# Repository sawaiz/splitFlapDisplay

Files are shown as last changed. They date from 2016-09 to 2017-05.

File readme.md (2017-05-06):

# Split Flap Display
Train stations and airports used to be riddled with these before LCD displays and monitors became commonplace. They used to show the departing and arrival scheduled as well as any delays but they fell out of favour due to the ease and creativity afforded with newer display technologies. What you lose along with that is the riffle sound that draws the eye when something changes, low power consumption, and unsurpassed visibility.

They are also referred to by genericised trademarks such as *Solari boards* after Solari di Udine, or *Pragoton* after the Czech manufacturer. New ones are no longer made and old ones under heavy disuse seldom show up on eBay and cost in the thousands per character, for a likely non-working one.

This project acts as a modern, modular, easy to interface alternative to finding vintage terminal displays. The goal is to have medium run (~100) production costs to near 10-15 USD/module.

## Module
The frame is laser cut acrylic, thickness is kept low and with a few modifications it can be made to injection mould and snap together. Currently, solvent welded. Electronics are mounded with screws, and communication occurs through pogo pins. Magnets connect modules to each other, and their polarity and positioning make sure it can only be plugged in properly. A magnet is also on the great wheel and is used for homing.

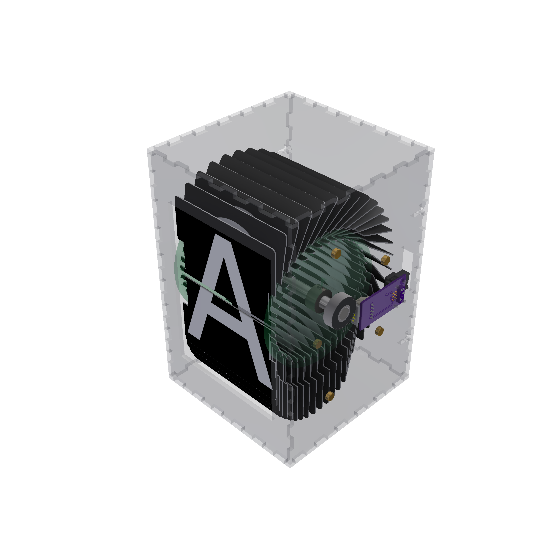
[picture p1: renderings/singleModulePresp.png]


The male pins can be seen on this side along with the gears, motor and main hub. Main shaft is mounted in inexpensive skateboard bearings and gears are those popularised by 3D printers, therefore prices are always falling. GT2 belts, collar clamps and 8mm hardened shaft also fall under that category.

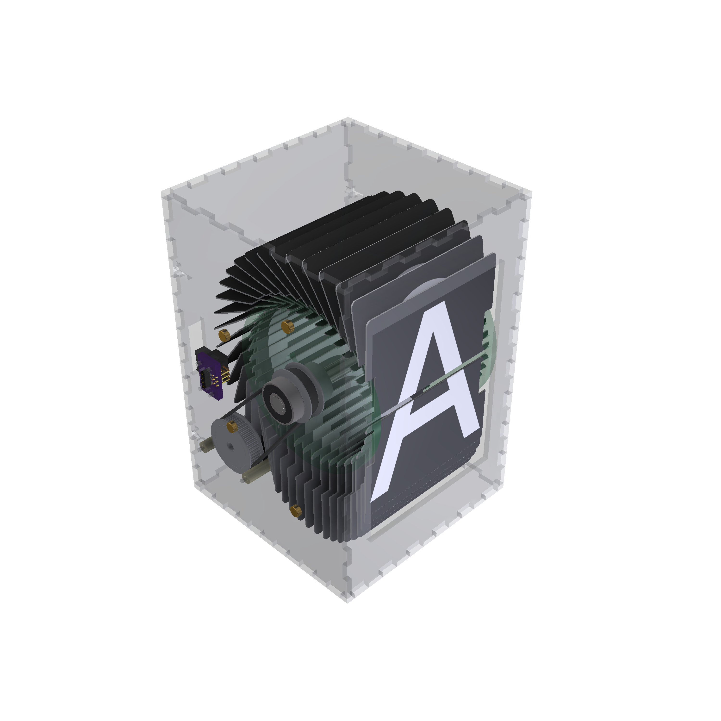
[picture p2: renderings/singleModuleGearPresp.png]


The "flaps" are based on die cut notches in plastic card blanks. Many vendors will print and die cut large quantities of cards, making scaling simple and labour intensive. Font and spacing can be changed, but as the goal is visibility, a san-serif monospaced font should be used. 

## Electronics
PCB and layout files found under electronics. Runs on a ATtiny13A, hall sensor for angular feedback, and a Darlington array for controlling the stepper. Under 5 USD in parts for medium volumes including the motor and pogo pins.

The two boards, in/out are connected with a ribbon able and IDC connectors (think PATA hard drives), inexpensive, easy to crimp... and even available pre-crimped in 4/6" lengths.

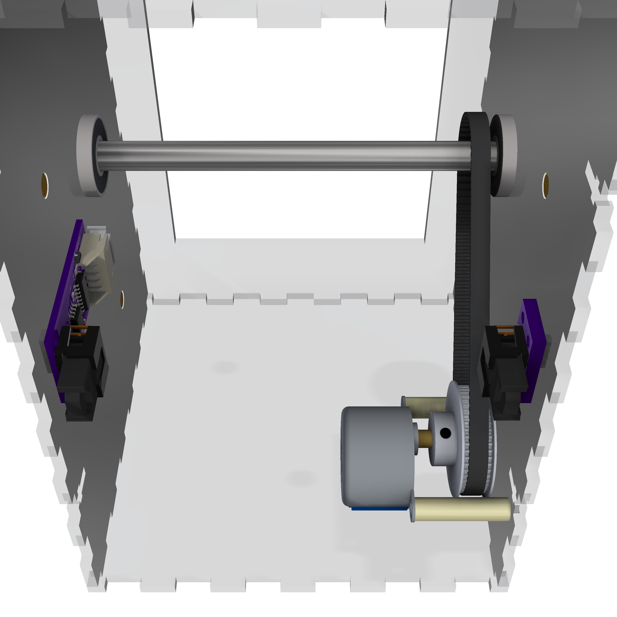
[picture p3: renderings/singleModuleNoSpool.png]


TODO: Schematic/layout images, BOM

### Firmware
AVR firmware along with makefile under firmware directory. On start it rotates to home, and then acts as a shift register forwarding the last character given

TODO: Insert communication clock diagram
TODO: Walk through code, decently commented, but avr ports are confusing

[singleModulePresp]: renderings/singleModulePresp.png "Assembled view"
[singleModuleGearPresp]: renderings/singleModuleGearPresp.png "Gear side view"
[singleModuleNoSpool]: renderings/singleModuleNoSpool.png "Detail of electronics with spool removed"

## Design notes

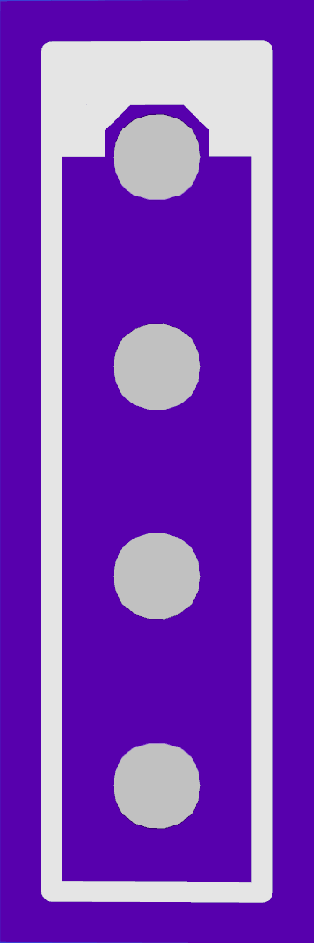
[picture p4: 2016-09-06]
electronics/cad/landing/back.png

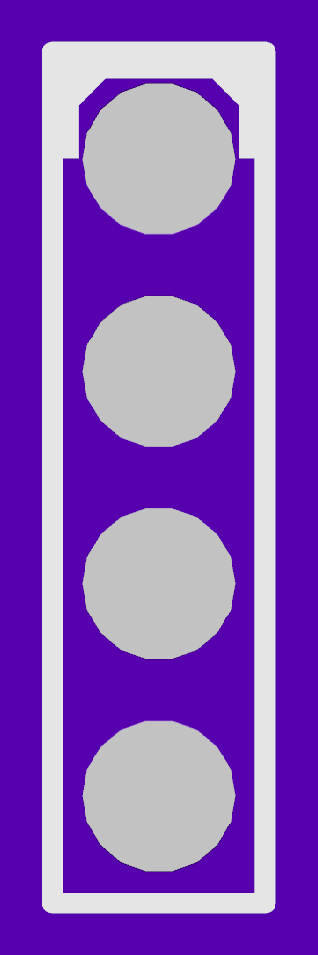
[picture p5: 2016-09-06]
electronics/cad/landing/front.png

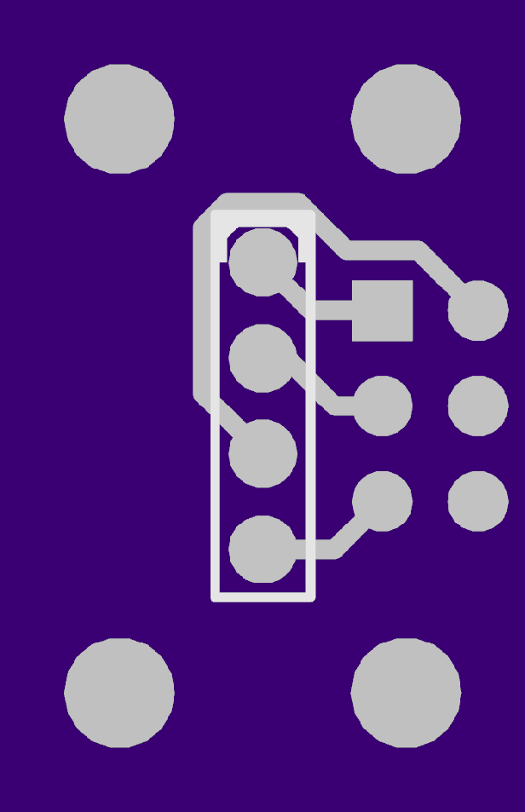
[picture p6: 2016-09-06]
electronics/cad/spring/back.png

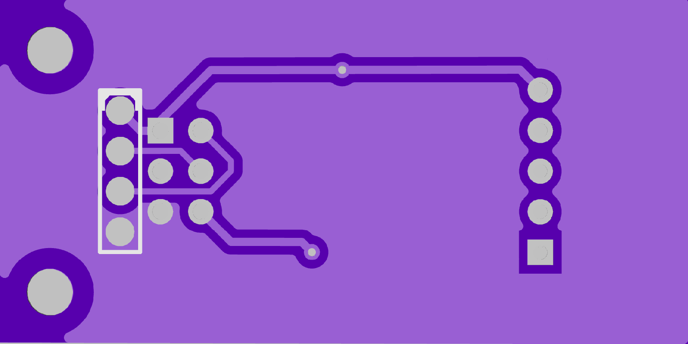
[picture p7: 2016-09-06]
electronics/cad/uC/back.png

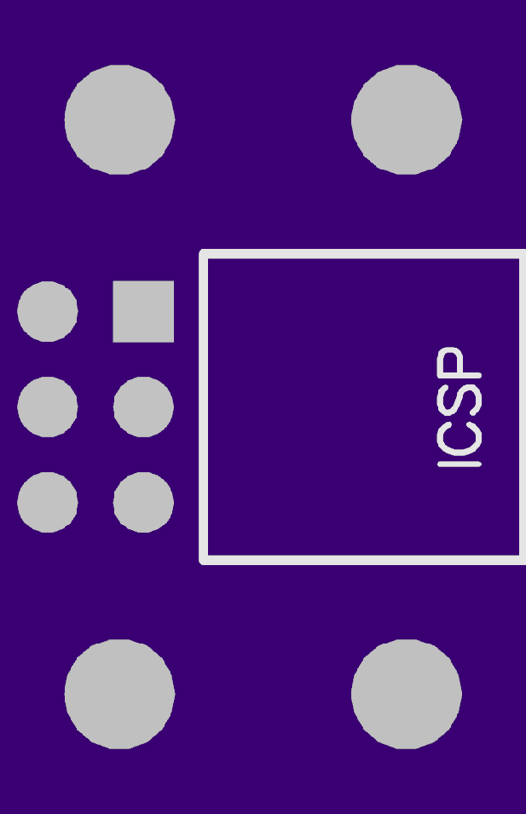
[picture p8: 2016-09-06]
electronics/cad/spring/front.png

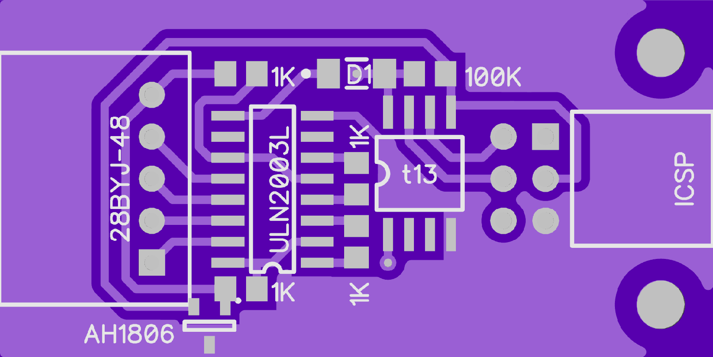
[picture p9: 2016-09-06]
electronics/cad/uC/front.png

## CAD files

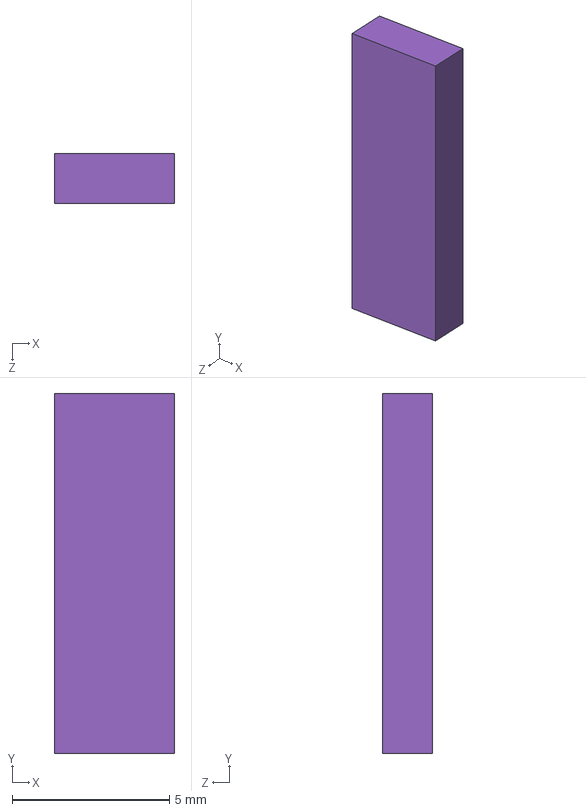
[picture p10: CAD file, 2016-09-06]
electronics/cad/landing/landing.step
3.81 x 11.4 x 1.60 mm

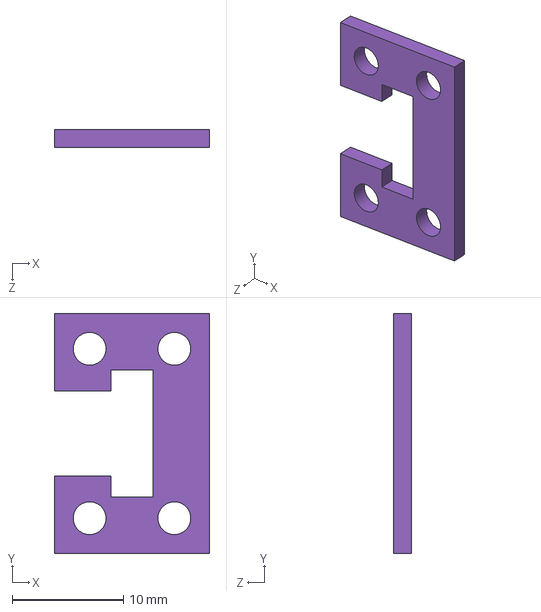
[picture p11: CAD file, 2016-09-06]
electronics/cad/spring/spacer.step
14.0 x 21.6 x 1.60 mm

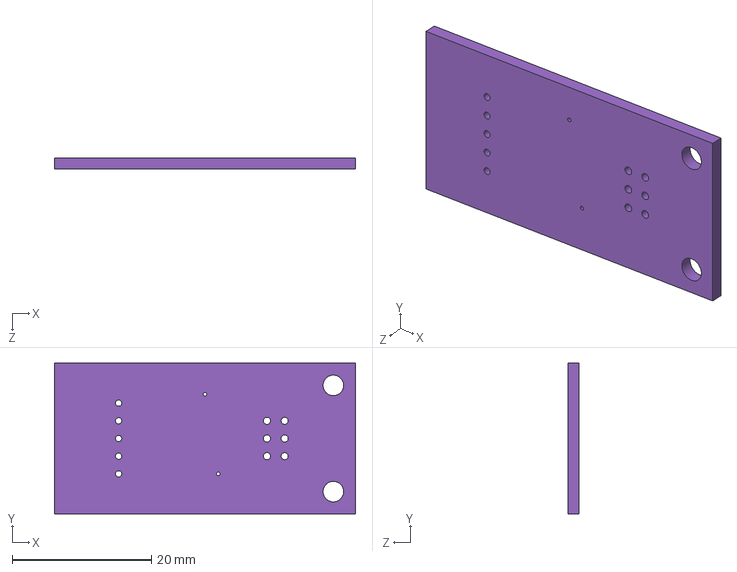
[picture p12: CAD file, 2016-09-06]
electronics/cad/uC/uC.step
43.2 x 21.6 x 1.60 mm

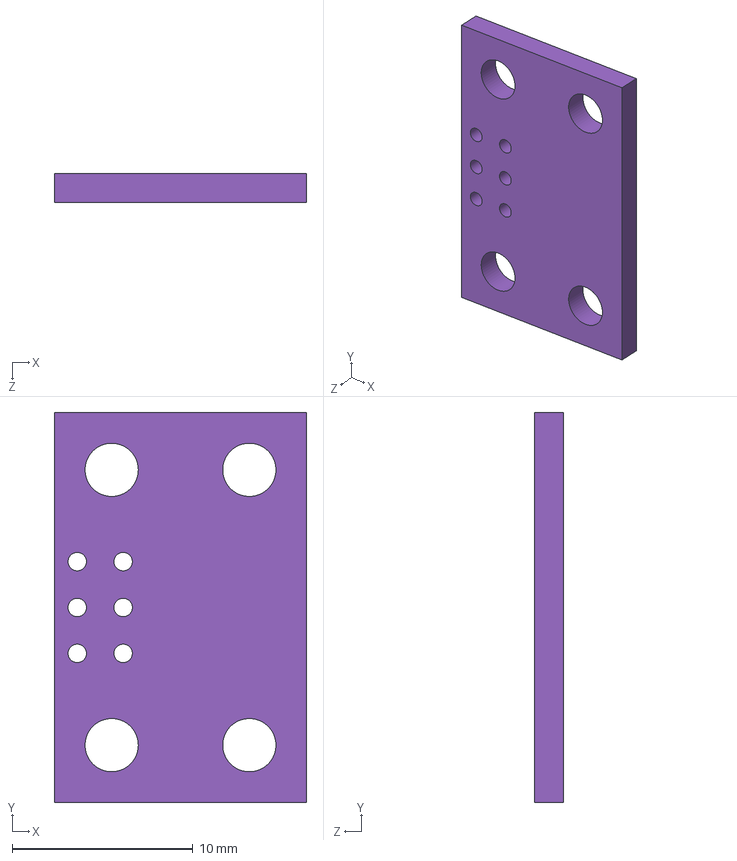
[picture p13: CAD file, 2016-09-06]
electronics/cad/spring/spring.step
14.0 x 21.6 x 1.60 mm

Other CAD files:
spoolGearSide.dwg
panelsWithKerf.dwg
cards/card-01.ipt
cards/card-02.ipt
cards/card-03.ipt
cards/card-04.ipt
cards/card-05.ipt
cards/card-06.ipt
cards/card-07.ipt
cards/card-08.ipt
cards/card-09.ipt
cards/card-10.ipt
cards/card-11.ipt
cards/card-12.ipt
cards/card-13.ipt
cards/card-14.ipt
cards/card-15.ipt
cards/card-16.ipt
cards/card-17.ipt
cards/card-18.ipt
cards/card-19.ipt
cards/card-20.ipt
cards/card-21.ipt
cards/card-22.ipt
cards/card-23.ipt
cards/card-24.ipt
cards/card-25.ipt
cards/card-26.ipt
cards/card-27.ipt
cards/card-28.ipt
cards/card-29.ipt
cards/card-30.ipt
cards/card-31.ipt
cards/card-32.ipt
cards/card-33.ipt
cards/card-34.ipt
cards/card-35.ipt
cards/card-36.ipt
cards/card-37.ipt
cards/card-38.ipt
cards/card-39.ipt
cards/card-40.ipt
cards/card.ipt
drive/8mmShaftCollar.ipt
drive/axleSpacer.ipt
drive/belt.ipt
drive/centeralShaft.ipt
drive/drive.iam
drive/gt236Tooth.ipt
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

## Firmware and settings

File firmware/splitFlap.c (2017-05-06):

// splitFlap.c
// Sawaiz

#include <avr/io.h>
#include <util/delay.h>
#include <avr/interrupt.h>

// Motor and Sensor
#define motorPinA PINB3
#define motorPinB PINB4
#define hallSensorPin PINB0
// Data Transfer
#define dataInPin PINB0
#define dataOutPin PINB2
#define clockPin PINB1

// All pins are on Port B
#define motorPortA PORTB
#define motorPortB PORTB
#define hallSensorPort PORTB
#define dataInPort PORTB
#define dataOutPort PORTB
#define clockPort PORTB

// All pins are on Port B
#define motorDirPortA DDRB
#define motorDirPortB DDRB
#define hallSensorDirPort DDRB
#define dataInDirPort DDRB
#define dataOutDirPort DDRB
#define clockDirPort DDRB

//inputs are on PINB
#define hallSensorPinAddress PINB
#define dataInPinAddress PINB0

// Prototypes
void stepForward(int steps);
void enableInterupt();
void startTimer();
void home();

// Globals
volatile uint8_t motorPosition = 0;
volatile uint8_t charBuffer = 0;
volatile uint8_t currentChar = 0;

ISR(INT0_vect) {
  // Clock has been triggered
  // Bit shift buffer
  charBuffer <<= 1;
  // Zero gets shifted in, if the input is high, set it to 1
  if ((dataInPort >> dataInPin) & 1) {
    charBuffer |= 1;
  }
  // Set output to highest Bit
  if ((charBuffer >> 7) & 1) {
    dataOutPort |= (1 << dataOutPin);
  } else {
    dataOutPort &= ~(1 << dataOutPin);
  }
  // Reset timeout timer
  TCNT0 = 0;
}

// If the timer overflows, and data has changed, set the char
ISR(TIM0_OVF_vect) {
  if (charBuffer != currentChar) {
    // Move forward to set the char
    stepForward(20);
    // Set the current char
    currentChar = charBuffer;
  }
}

// Stepper motor
void stepForward(int steps) {
  int i = 0;
  for (i=0 ; i < steps; i++){
    if(motorPosition == 0 ){
      motorPortA &= ~(1 << motorPinA);
      motorPortB |= (1 << motorPinB);
      motorPosition++;
    } else if (motorPosition == 1){
      motorPortA |= (1 << motorPinA);
      motorPortB |= (1 << motorPinB);
      motorPosition++;
    } else if (motorPosition == 2){
      motorPortA |= (1 << motorPinA);
      motorPortB &= ~(1 << motorPinB);
      motorPosition++;      
    } else if (motorPosition == 3){
      motorPortA &= ~(1 << motorPinA);
      motorPortB &= ~(1 << motorPinB);
      motorPosition = 0;
    }
    _delay_ms(5);
  }
}

// Enable clock interrupt
void enableInterupt() {
  // Enable Global Interrupts
  sei();
  // MCU Control Register  // Low  Change  Fall Rise
  MCUCR &= ~(1 << ISC00);  // 0    1       0    1
  MCUCR |= 1 << ISC01;     // 0    0       1    1
  // GIMSK – General Interrupt Mask Register
  GIMSK |= 1 << INT0;
}

// Start timer
void startTimer() {
  // Connect timer to system clk  
  // Sets the timeout, ex: 1MHz clk, 1us * 256 (8 bit timer) * 8 (prescalar)
  // Enable prescalar     // stop clk clk/8  clk/64 clk/256 clk/1024
  TCCR0B &= ~(1 << CS00); // 0    1   0      1       0      1
  TCCR0B &= ~(1 << CS01); // 0    0   1      1       0      0
  TCCR0B |= (1 << CS02);  // 0    0   0      0       1      1
  // Enable Global Interrupts
  sei();
  // Enable timer overflow interupt
  TIMSK0 |= (1 << TOIE0);
}

// Home the wheel
void home() {
  // If the pin is high, try again
  while (hallSensorPinAddress & (1 << hallSensorPin)) {
    // If the hall sensor is not activated
    stepForward(1);
  }
  // Then move to the blank character
  stepForward(400);
}

int main() {
  // Motor and data out are output
  motorDirPortA |= 1 << motorPinA;
  motorDirPortB |= 1 << motorPinB;
  dataOutDirPort |= 1 << dataOutPin;
  // Hall sensor, clock, and dataIn inputs
  hallSensorDirPort &= ~(1 << hallSensorPin);
  clockDirPort &= ~(1 << clockPin);
  dataInDirPort &= ~(1 << dataInPin);

  // Home the wheel
  home();

  // Enable interrupts to start accepting data.
  enableInterupt();

  // Hang out and wait for interupts
  while (1) {
    // stepForward(400);
  }

  // Program should never make it here, so error out
  return 1;
}

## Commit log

2015-10-05 Initital Commit
    [608RS.ipt, axleSpacer.ipt, back.ipt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]
2015-10-06 Added magnets, assembly is so slow now.
    [back.ipt, belt.ipt, card-01.ipt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]
2016-09-06 Electroincs setup proerly, ready for build... i think
    [1 by 4.iam, 1x1.iam, 1x4.iam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]
2016-09-07 Added pattrens changed size so it fits
    [back.ipt, belt.ipt, card-01.ipt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]
2017-05-06 Wrote makefile, included renders, removed showcase, blender
    [1 by 4.iam, 608RS.ipt, 61200623021.ipt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]
